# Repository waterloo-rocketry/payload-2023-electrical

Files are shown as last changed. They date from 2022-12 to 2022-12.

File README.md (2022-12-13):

WELCOME TO PAYLOAD: "NOT QUITE DEPLOYABLE"

Here is the folder in the google drive where most of our research happens (if you don't have access, and need it, ask!)
https://drive.google.com/drive/folders/1Cd6_AShmbkWPmAZkzhvAZI7hbHMKju_5?usp=sharing

If you can't find the project you're looking for, make sure to check the branches

CONFLUENCE (but don't expect it to be updated)
https://uwaterloo.atlassian.net/wiki/spaces/ROCKETRY/pages/42574873580/Payload

**How to Start Editing Schematics**
- Clone the "canhw" repo from https://github.com/waterloo-rocketry/canhw
- Enter canhw and make sure you are on the most up to date version of master branch
- Make sure that both the payload-2023-electrical and canhw repos are in the same parent directory! KiCAD will not be able to find our custom libraries otherwise

# 2023 Electrical Overview
Please see the updated .drawio file, which contains a detailed electrical block diagram

The 2023 electrical system is made up of 5 boards:

### GPS board
- Can be found at https://github.com/waterloo-rocketry/canhw/tree/master/gps
- GPS is a very simple board. It gets data from a GPS reciever and forwards it over CAN. 
- Data from GPS board will be the x/y position measurement input to state estimation
- A copy will be mounted on GrandPapa

### Logger board
- Can be found at https://github.com/waterloo-rocketry/canhw/tree/master/logger
- Logger is also a very simple board. It reads in all the CAN messages it sees and saves them to an SD card
- Logger is extremely useful for all sorts of diagnostics, but will allow us to collect all the sensor data as the rocket flies, do some post-flight analysis, and hopefully figure out if state estimation did a good job
- A copy will be mounted on GrandPapa

### Minisensor
- Can be found at https://github.com/waterloo-rocketry/canhw/tree/master/sensor_mini 
- Minisensor gets data from an altimeter, IMU (an accelerometer, magnetometer, and gyroscope packed into one chip) and optionally one or more pressure transmitters, RTDs, strain gauges, the list goes on (there are some generic amplifier circuits that have a variety of uses).
- For its application to payload, we only care about the IMU and altimeter, which provide most of the data to state estimation
- Will be wired to GrandPapa to maximize flexibility and because there's no more space on it lol

### COTS PIC Dev Board (DM320209)
- Datasheet can be found at http://ww1.microchip.com/downloads/en/DeviceDoc/Curiosity_PIC32MZEF2.0_Development_Board_Users_Guide_DS70005400A.pdf
- This beefy boy runs state estimation cause we did not have time to design a second board from scratch and matrix multiplication (which is basically what state estimation is) is really computationally intensive. An NVIDIA GeForce RTX 4090 GPU was proposed as an alternative but was ultimately struck down because "it would cost double payload's yearly budget" and "doesn't obey the 3U Cubesat standard".

### GrandPapa
- Can be found RIGHT HERE under "/GrandPapa_Board"
- GrandPapa is our power management, battery charging, and communications board. It pulls from the rocket to power the payload's systems, and pulls from the payload's battery supply when external power is no longer available. It also manages communication between RocketCAN (the rocket's main communication network) and the payload's internal network. Because CAN is a broadcast protocol (every board sees every message on the network all the time), and payload will be constantly transmitting sensor data, we do not want those messages interfering with whatever is happening on RocketCAN or vice versa
- See the schamtic notes for details on the power path

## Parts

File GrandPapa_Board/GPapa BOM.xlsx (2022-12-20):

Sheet: GrandPapa_Board_20221209
Column1 | Column2 | Column3 | Column4 | Column5 | Column6 | Column7
Source: | C:\Users\joedo\Documents\UW Rocketry\payload-2023-electrical\GrandPapa_Board\GrandPapa_Board.kicad_sch
Date: | 2022-12-09 12:44:19 PM
Tool: | Eeschema (6.0.5)
Generator: | C:\Program Files\KiCad\6.0\bin\scripting\plugins/bom_csv_grouped_by_value_with_fp.py
Component Count: | 94
Ref | Qnty | Value | Cmp name | Footprint | Description | In Stock In Bay
C1, C2, C5, C22, C23, | 5 | 10uF | C_Small | Capacitor_SMD:C_0805_2012Metric_Pad1.18x1.45mm_HandSolder | Unpolarized capacitor, small symbol | 43 in the bay
C3, C6, C12, C13, C14, C21, | 6 | 0.1uF | C_Small | Capacitor_SMD:C_0805_2012Metric_Pad1.18x1.45mm_HandSolder | Unpolarized capacitor, small symbol | 100+ in the bay
C4, | 1 | 5nF | C_Small | Capacitor_SMD:C_0805_2012Metric_Pad1.18x1.45mm_HandSolder | Unpolarized capacitor, small symbol | 0
C7, C9, C10, C11, | 4 | 4.7uF | C | Capacitor_SMD:C_0805_2012Metric_Pad1.18x1.45mm_HandSolder | Unpolarized capacitor | 50~ in the Bay
C8, | 1 | 25pF | C_Small | Capacitor_SMD:C_0805_2012Metric_Pad1.18x1.45mm_HandSolder | Unpolarized capacitor, small symbol | 25 in the Bay
C15, | 1 | 44 uF | C_Small | Capacitor_SMD:C_0805_2012Metric_Pad1.18x1.45mm_HandSolder | Unpolarized capacitor, small symbol | 0
C16, C17, | 2 | 27pF | C_Small | Capacitor_SMD:C_0805_2012Metric_Pad1.18x1.45mm_HandSolder | Unpolarized capacitor, small symbol | 100+ in the Bay
C18, C19, | 2 | 0.1uF 20V | C_Small | Capacitor_SMD:C_0805_2012Metric_Pad1.18x1.45mm_HandSolder | Unpolarized capacitor, small symbol | 49 in the bay
D1, D5, D8, | 3 | 150120BS75000 | LED | LED_SMD:LED_1206_3216Metric_Pad1.42x1.75mm_HandSolder | Light emitting diode | 100+ in bay
D3, D6, | 2 | QBLP650-IW | LED | LED_SMD:LED_1206_3216Metric_Pad1.42x1.75mm_HandSolder | Light emitting diode | 100+ in bay
D4, D7, | 2 | 156120RS75000 | LED | LED_SMD:LED_1206_3216Metric_Pad1.42x1.75mm_HandSolder | Light emitting diode | 100+ in bay
F1, F3, | 2 | 1.5A | Polyfuse | Fuse:Fuse_0805_2012Metric_Pad1.15x1.40mm_HandSolder | Resettable fuse, polymeric positive temperature coefficient
F2, | 1 | 1.2A | Polyfuse | Fuse:Fuse_0805_2012Metric_Pad1.15x1.40mm_HandSolder | Resettable fuse, polymeric positive temperature coefficient
H1, H2, H3, H4, H5, H6, H7, H8, | 8 | MountingHole_Pad | MountingHole_Pad | MountingHole:MountingHole_3.5mm_Pad_Via | Mounting Hole with connection | N/A
J1, | 1 | 3.7V LiPo Single Cell | Conn_01x02_Female | Connector_JST:JST_PH_S2B-PH-K_1x02_P2.00mm_Horizontal | Generic connector, single row, 01x02, script generated (kicad-library-utils/schlib/autogen/connector/)
J2, | 1 | HARWIN_ROCKET | Conn_01x05 | PapaOld:connector_Harwin_M80-5000642 | Generic connector, single row, 01x05, script generated (kicad-library-utils/schlib/autogen/connector/) | N/A
J3, | 1 | Dupont_GPS | Conn_01x06_Female | PapaOld:connector_Harwin_M80-5000642 | Generic connector, single row, 01x06, script generated (kicad-library-utils/schlib/autogen/connector/)
J4, | 1 | HARWIN_MINISENSOR | Conn_01x05 | PapaOld:connector_Harwin_M80-5000642 | Generic connector, single row, 01x05, script generated (kicad-library-utils/schlib/autogen/connector/) | N/A
J5, | 1 | Dupont_Logger | Conn_01x06_Female | PapaOld:connector_Harwin_M80-5000642 | Generic connector, single row, 01x06, script generated (kicad-library-utils/schlib/autogen/connector/)
J6, | 1 | Prog Header | Conn_01x05_Female | Connector_PinHeader_2.54mm:PinHeader_1x05_P2.54mm_Vertical | Generic connector, single row, 01x05, script generated (kicad-library-utils/schlib/autogen/connector/)
J7, | 1 | HARWIN_KALMAN | Conn_01x05 | PapaOld:connector_Harwin_M80-5000642 | Generic connector, single row, 01x05, script generated (kicad-library-utils/schlib/autogen/connector/) | N/A
J11, | 1 | Dupont 01x04_Male | Conn_01x04_Male | Connector_PinHeader_2.54mm:PinHeader_1x04_P2.54mm_Vertical | Generic connector, single row, 01x04, script generated (kicad-library-utils/schlib/autogen/connector/)
L1, | 1 | 5.6uH | L | Inductor_SMD:L_Vishay_IHLP-2020 | Inductor | ORD
L2, | 1 | 4.7uH | L_Small | Inductor_SMD:L_Sumida_CDMC6D28_7.25x6.5mm | Inductor, small symbol | ORD
R1, R23, | 2 | 20mR | R_US | Resistor_SMD:R_1206_3216Metric_Pad1.30x1.75mm_HandSolder | Resistor, US symbol
R2, | 1 | 1MR | R_Small_US | Resistor_SMD:R_0805_2012Metric_Pad1.20x1.40mm_HandSolder | Resistor, small US symbol
R3, R12, R13, R15, | 4 | 100R | R_Small_US | Resistor_SMD:R_0805_2012Metric_Pad1.20x1.40mm_HandSolder | Resistor, small US symbol
R4, | 1 | 2kR | R_Small_US | Resistor_SMD:R_0805_2012Metric_Pad1.20x1.40mm_HandSolder | Resistor, small US symbol
R5, | 1 | 25kR | R_Small_US | Resistor_SMD:R_0805_2012Metric_Pad1.20x1.40mm_HandSolder | Resistor, small US symbol
R6, R20, R21, | 3 | 470R | R_Small_US | Resistor_SMD:R_0805_2012Metric_Pad1.20x1.40mm_HandSolder | Resistor, small US symbol
R7, | 1 | 500R | R_US | Resistor_SMD:R_0805_2012Metric_Pad1.20x1.40mm_HandSolder | Resistor, US symbol
R8, R11, R17, R18, R26, | 5 | 10kR | R_Small_US | Resistor_SMD:R_0805_2012Metric_Pad1.20x1.40mm_HandSolder | Resistor, small US symbol
R9, R10, R22, R24, | 4 | 0 | R_Small_US | Resistor_SMD:R_0805_2012Metric_Pad1.20x1.40mm_HandSolder | Resistor, small US symbol
R14, | 1 | 150R | R_Small_US | Resistor_SMD:R_0805_2012Metric_Pad1.20x1.40mm_HandSolder | Resistor, small US symbol
R16, | 1 | 11kR | R_Small_US | Resistor_SMD:R_0805_2012Metric_Pad1.20x1.40mm_HandSolder | Resistor, small US symbol
R19, | 1 | 70kR | R_Small_US | Resistor_SMD:R_0805_2012Metric_Pad1.20x1.40mm_HandSolder | Resistor, small US symbol
R25, | 1 | 324kR | R_Small_US | Resistor_SMD:R_0805_2012Metric_Pad1.20x1.40mm_HandSolder | Resistor, small US symbol
R27, | 1 | 15kR | R_US | Resistor_SMD:R_0805_2012Metric_Pad1.20x1.40mm_HandSolder | Resistor, US symbol
TH1, | 1 | 10k | Thermistor_NTC | Resistor_SMD:R_0805_2012Metric_Pad1.20x1.40mm_HandSolder | Temperature dependent resistor, negative temperature coefficient | ORD
TP1, TP2, TP3, TP4, TP7, | 5 | TestPoint | TestPoint | Connector_PinHeader_2.54mm:PinHeader_1x01_P2.54mm_Vertical | test point
U1, | 1 | MCP1642B-50I/MS | MCP1642B{slash}D-xx | Package_SO:MSOP-8_3x3mm_P0.65mm | Fixed Output Boost Regulator | ORD
U2, | 1 | BD9E302EFJ | BD9E302EFJ | Package_SO:HTSOP-8-1EP_3.9x4.9mm_P1.27mm_EP2.4x3.2mm |  | ORD
U3, | 1 | MCP73871T-1CCI/ML | MCP73871 | Package_DFN_QFN:QFN-20-1EP_4x4mm_P0.5mm_EP2.5x2.5mm | Single cell, Li-Ion/Li-Po charge management controller | ORD
U4, U6, | 2 | INA180 | INA180 | Package_TO_SOT_SMD:SOT-23-5_HandSoldering | Low- and High-Side Voltage Output, Current-Sense Amplifier
U5, | 1 | FPF2124 | FPF2124 | Package_TO_SOT_SMD:SOT-23-5_HandSoldering |  | ORD
U7, U8, | 2 | MCP2562-E/SN | MCP2562 | Package_SO:SOIC-8_3.9x4.9mm_P1.27mm | High-Speed CAN Transceiver
U9, | 1 | PIC18F26K83 | PIC18F26K83 | Package_SO:SSOP-28_5.3x10.2mm_P0.65mm | 28-Pin, Low-Power, High-Performance Microcontrollers with CAN Technology
U10, | 1 | MCP2515-I/P | MCP2515 | Package_SO:SOIC-18W_7.5x11.6mm_P1.27mm |  | ORD
Y1, | 1 | 12MHz | Crystal | Crystal:Crystal_HC49-4H_Vertical | Two pin crystal | IN STOCK

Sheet: GrandPapa_Board_2022_12_14
_ | Column2 | Column3 | Column4 | Column5 | Column6 | Column7 | Column8
Source: | C:\Users\joedo\Documents\UW Rocketry\payload-2023-electrical\GrandPapa_Board\GrandPapa_Board.kicad_sch
Date: | 2022-12-14 7:13:50 AM
Tool: | Eeschema (6.0.5)
Generator: | C:\Program Files\KiCad\6.0\bin\scripting\plugins/bom_csv_grouped_by_value_with_fp.py
Component Count: | 97
Ref | Qnty | Value | Cmp name | Footprint | Description | In Stock | In Order
C1, C2, C5, C22, C23, | 5 | 10uF | C_Small | Capacitor_SMD:C_0805_2012Metric_Pad1.18x1.45mm_HandSolder | Unpolarized capacitor, small symbol | 43 in the bay | Y
C3, C6, C12, C13, C14, C21, | 6 | 0.1uF | C_Small | Capacitor_SMD:C_0805_2012Metric_Pad1.18x1.45mm_HandSolder | Unpolarized capacitor, small symbol | 100+ in the bay | Y
C4, | 1 | 5nF | C_Small | Capacitor_SMD:C_0805_2012Metric_Pad1.18x1.45mm_HandSolder | Unpolarized capacitor, small symbol | 0 | Y
C7, C9, C10, C11, | 4 | 4.7uF | C | Capacitor_SMD:C_0805_2012Metric_Pad1.18x1.45mm_HandSolder | Unpolarized capacitor | 50~ in the Bay
C8, | 1 | 25pF | C_Small | Capacitor_SMD:C_0805_2012Metric_Pad1.18x1.45mm_HandSolder | Unpolarized capacitor, small symbol | 25 in the Bay
C15, | 1 | 44 uF | C_Small | Capacitor_SMD:C_0805_2012Metric_Pad1.18x1.45mm_HandSolder | Unpolarized capacitor, small symbol | 0 | Y
C16, C17, | 2 | 27pF | C_Small | Capacitor_SMD:C_0805_2012Metric_Pad1.18x1.45mm_HandSolder | Unpolarized capacitor, small symbol | 100+ in the Bay
C18, C19, | 2 | 0.1uF 20V | C_Small | Capacitor_SMD:C_0805_2012Metric_Pad1.18x1.45mm_HandSolder | Unpolarized capacitor, small symbol | 49 in the bay
D1, D5, D8, | 3 | 150120BS75000 | LED | LED_SMD:LED_1206_3216Metric_Pad1.42x1.75mm_HandSolder | Light emitting diode | 100+ in bay
D3, D6, | 2 | QBLP650-IW | LED | LED_SMD:LED_1206_3216Metric_Pad1.42x1.75mm_HandSolder | Light emitting diode | 100+ in bay
D4, D7, | 2 | 156120RS75000 | LED | LED_SMD:LED_1206_3216Metric_Pad1.42x1.75mm_HandSolder | Light emitting diode | 100+ in bay
F1, F2, F3, | 3 | 1.5A | Polyfuse | Fuse:Fuse_1812_4532Metric_Pad1.30x3.40mm_HandSolder | Resettable fuse, polymeric positive temperature coefficient |  | Y
H1, H2, H4, H5, | 4 | MountingHole_Pad | MountingHole_Pad | MountingHole:MountingHole_3.2mm_M3_Pad | Mounting Hole with connection | N/A
H3, H6, H7, H8, | 4 | MountingHole_Pad | MountingHole_Pad | MountingHole:MountingHole_3.5mm_Pad_Via | Mounting Hole with connection | N/A
J1, | 1 | 3.7V LiPo Single Cell | Conn_01x02_Female | Connector_JST:JST_PH_S2B-PH-K_1x02_P2.00mm_Horizontal | Generic connector, single row, 01x02, script generated (kicad-library-utils/schlib/autogen/connector/)
J2, | 1 | HARWIN_ROCKET | Conn_01x05 | PapaOld:connector_Harwin_M80-5000642 | Generic connector, single row, 01x05, script generated (kicad-library-utils/schlib/autogen/connector/) | N/A
J3, | 1 | Dupont_GPS | Conn_01x06_Female | PapaOld:connector_Harwin_M80-5000642 | Generic connector, single row, 01x06, script generated (kicad-library-utils/schlib/autogen/connector/)
J4, | 1 | HARWIN_MINISENSOR | Conn_01x05 | PapaOld:connector_Harwin_M80-5000642 | Generic connector, single row, 01x05, script generated (kicad-library-utils/schlib/autogen/connector/) | N/A
J5, | 1 | Dupont_Logger | Conn_01x06_Female | PapaOld:connector_Harwin_M80-5000642 | Generic connector, single row, 01x06, script generated (kicad-library-utils/schlib/autogen/connector/)
J6, | 1 | PROG Header | Conn_01x05_Female | Connector_PinHeader_2.54mm:PinHeader_1x05_P2.54mm_Vertical | Generic connector, single row, 01x05, script generated (kicad-library-utils/schlib/autogen/connector/)
J7, | 1 | HARWIN_KALMAN | Conn_01x05 | PapaOld:connector_Harwin_M80-5000642 | Generic connector, single row, 01x05, script generated (kicad-library-utils/schlib/autogen/connector/) | N/A
J8, | 1 | Therm EN Jumper | Conn_01x03_Male | Connector_PinHeader_2.54mm:PinHeader_1x03_P2.54mm_Vertical | Generic connector, single row, 01x03, script generated (kicad-library-utils/schlib/autogen/connector/) |  | Y
J11, | 1 | Dupont 01x04_Male | Conn_01x04_Male | Connector_PinHeader_2.54mm:PinHeader_1x04_P2.54mm_Vertical | Generic connector, single row, 01x04, script generated (kicad-library-utils/schlib/autogen/connector/)
L1, | 1 | 5.6uH | L | Inductor_SMD:L_Vishay_IHLP-2020 | Inductor |  | Y
L2, | 1 | 4.7uH | L_Small | Inductor_SMD:L_Sumida_CDMC6D28_7.25x6.5mm | Inductor, small symbol |  | Y
R1, R23, | 2 | 20mR | R_US | Resistor_SMD:R_1206_3216Metric_Pad1.30x1.75mm_HandSolder | Resistor, US symbol
R2, | 1 | 1MR | R_Small_US | Resistor_SMD:R_0805_2012Metric_Pad1.20x1.40mm_HandSolder | Resistor, small US symbol |  | Y
R3, R12, R13, R15, | 4 | 100R | R_Small_US | Resistor_SMD:R_0805_2012Metric_Pad1.20x1.40mm_HandSolder | Resistor, small US symbol |  | Y
R4, R8, R11, R17, R18, R26, R29, | 7 | 10kR | R_Small_US | Resistor_SMD:R_0805_2012Metric_Pad1.20x1.40mm_HandSolder | Resistor, small US symbol
R5, | 1 | 25kR | R_Small_US | Resistor_SMD:R_0805_2012Metric_Pad1.20x1.40mm_HandSolder | Resistor, small US symbol |  | Y
R6, R20, R21, | 3 | 470R | R_Small_US | Resistor_SMD:R_0805_2012Metric_Pad1.20x1.40mm_HandSolder | Resistor, small US symbol
R7, | 1 | 500R | R_US | Resistor_SMD:R_0805_2012Metric_Pad1.20x1.40mm_HandSolder | Resistor, US symbol |  | Y
R9, R10, R22, R24, | 4 | 0 | R_Small_US | Resistor_SMD:R_0805_2012Metric_Pad1.20x1.40mm_HandSolder | Resistor, small US symbol
R14, | 1 | 150R | R_Small_US | Resistor_SMD:R_0805_2012Metric_Pad1.20x1.40mm_HandSolder | Resistor, small US symbol
R16, | 1 | 11kR | R_Small_US | Resistor_SMD:R_0805_2012Metric_Pad1.20x1.40mm_HandSolder | Resistor, small US symbol |  | Y
R19, | 1 | 70kR | R_Small_US | Resistor_SMD:R_0805_2012Metric_Pad1.20x1.40mm_HandSolder | Resistor, small US symbol |  | Y
R25, | 1 | 324kR | R_Small_US | Resistor_SMD:R_0805_2012Metric_Pad1.20x1.40mm_HandSolder | Resistor, small US symbol |  | Y
R27, | 1 | 15kR | R_US | Resistor_SMD:R_0805_2012Metric_Pad1.20x1.40mm_HandSolder | Resistor, US symbol
R28, | 1 | 2.5kR | R_Small_US | Resistor_SMD:R_0805_2012Metric_Pad1.20x1.40mm_HandSolder | Resistor, small US symbol |  | Y
TH1, | 1 | 10k | Thermistor_NTC | Resistor_SMD:R_0805_2012Metric_Pad1.20x1.40mm_HandSolder | Temperature dependent resistor, negative temperature coefficient |  | Y
TP1, TP2, TP3, TP4, TP7, | 5 | TestPoint | TestPoint | Connector_PinHeader_2.54mm:PinHeader_1x01_P2.54mm_Vertical | test point |  | Y
U1, | 1 | MCP1642B-50I/MS | MCP1642B{slash}D-xx | Package_SO:MSOP-8_3x3mm_P0.65mm | Fixed Output Boost Regulator |  | Y
U2, | 1 | BD9E302EFJ | BD9E302EFJ | Package_SO:HTSOP-8-1EP_3.9x4.9mm_P1.27mm_EP2.4x3.2mm |  |  | Y
U3, | 1 | MCP73871T-1CCI/ML | MCP73871 | Package_DFN_QFN:QFN-20-1EP_4x4mm_P0.5mm_EP2.5x2.5mm | Single cell, Li-Ion/Li-Po charge management controller |  | Y
U4, U6, | 2 | INA180 | INA180 | Package_TO_SOT_SMD:SOT-23-5_HandSoldering | Low- and High-Side Voltage Output, Current-Sense Amplifier
U5, | 1 | FPF2124 | FPF2124 | Package_TO_SOT_SMD:SOT-23-5_HandSoldering |  |  | Y
U7, U8, | 2 | MCP2562-E/SN | MCP2562 | Package_SO:SOIC-8_3.9x4.9mm_P1.27mm | High-Speed CAN Transceiver
U9, | 1 | PIC18F26K83 | PIC18F26K83 | Package_SO:SSOP-28_5.3x10.2mm_P0.65mm | 28-Pin, Low-Power, High-Performance Microcontrollers with CAN Technology
U10, | 1 | MCP2515-I/P | MCP2515 | Package_SO:SOIC-18W_7.5x11.6mm_P1.27mm
Y1, | 1 | 12MHz | Crystal | Crystal:Crystal_HC49-4H_Vertical | Two pin crystal

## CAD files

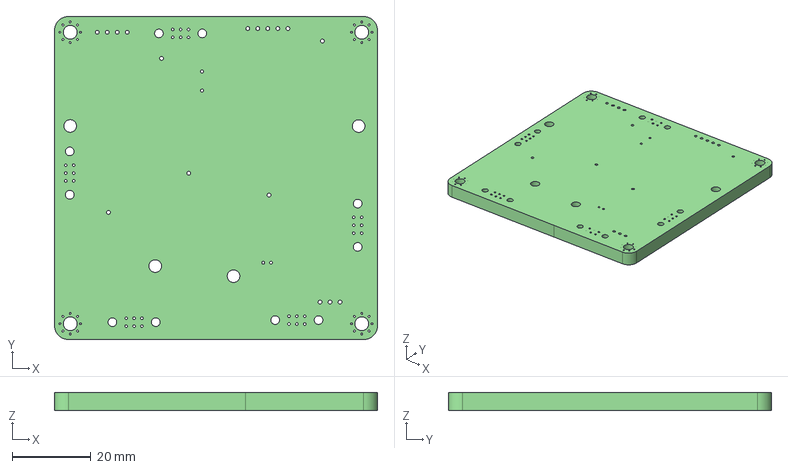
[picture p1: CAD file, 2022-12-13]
GrandPapa_Board/GrandPapa_Board.step
82.0 x 82.0 x 4.69 mm

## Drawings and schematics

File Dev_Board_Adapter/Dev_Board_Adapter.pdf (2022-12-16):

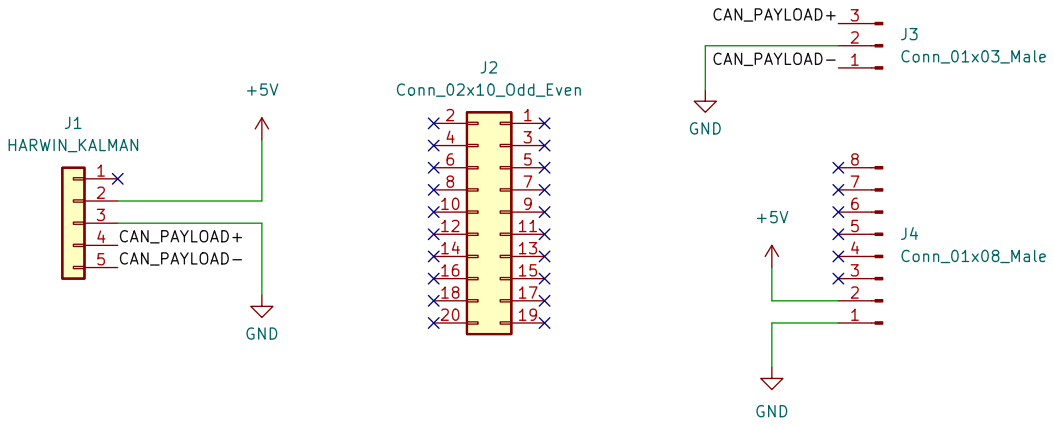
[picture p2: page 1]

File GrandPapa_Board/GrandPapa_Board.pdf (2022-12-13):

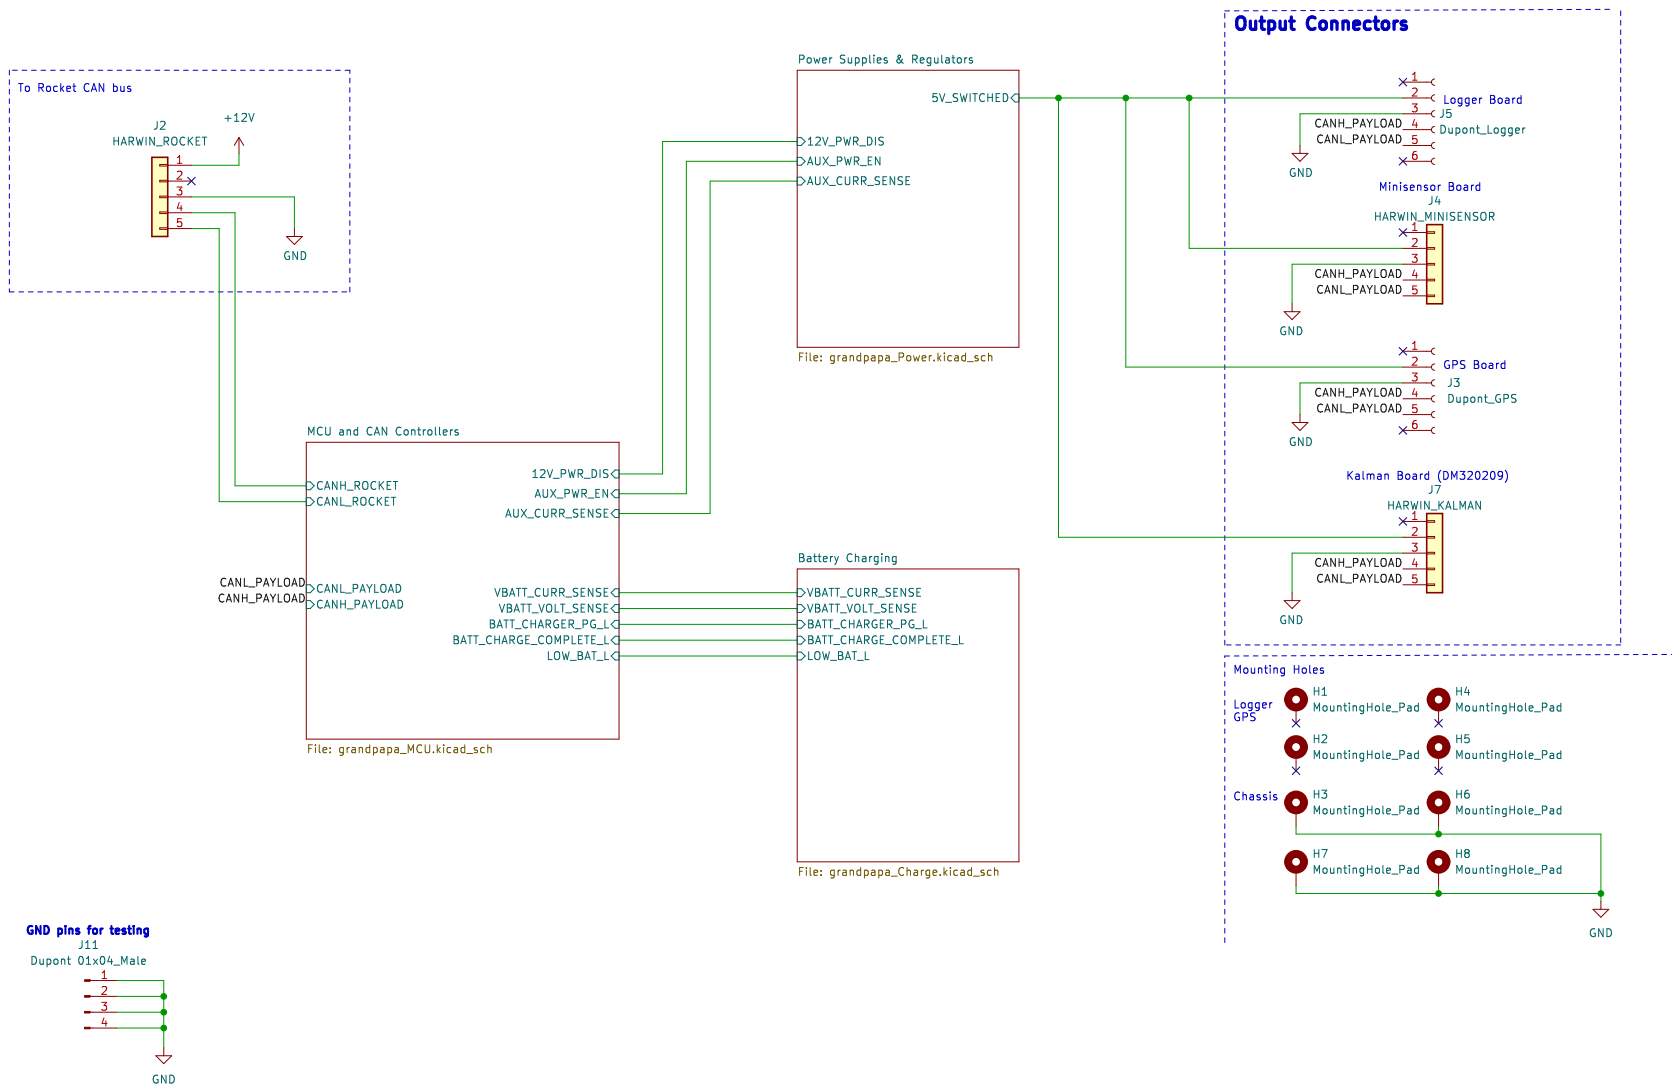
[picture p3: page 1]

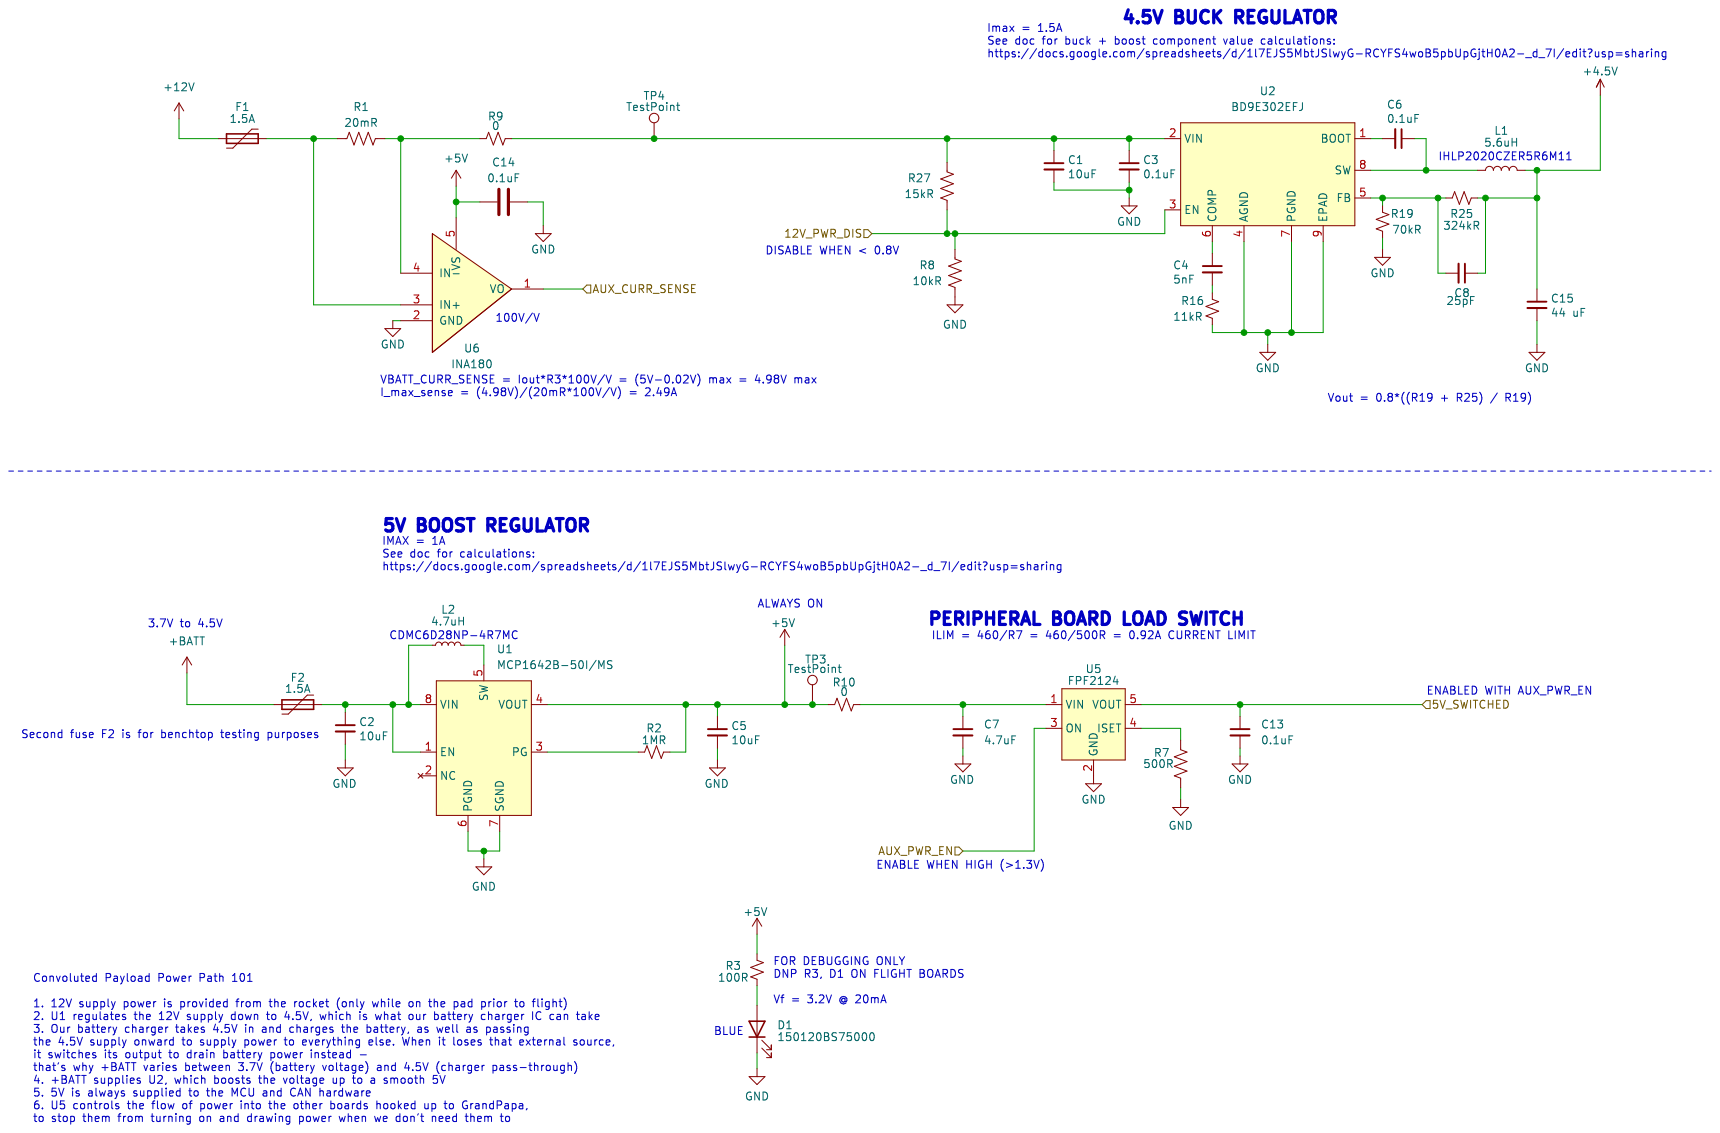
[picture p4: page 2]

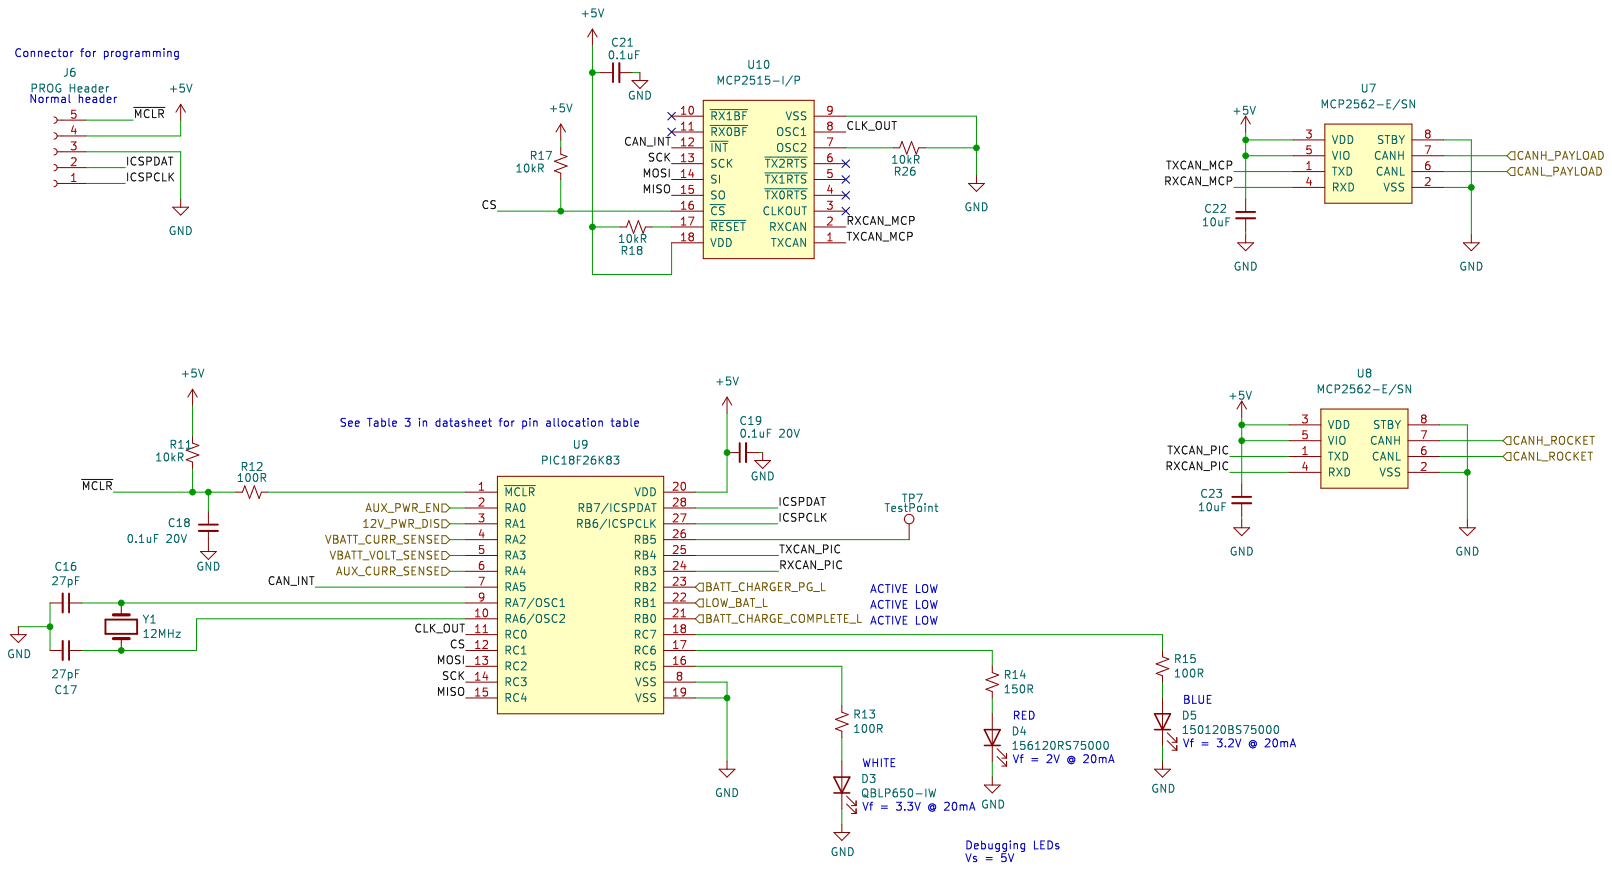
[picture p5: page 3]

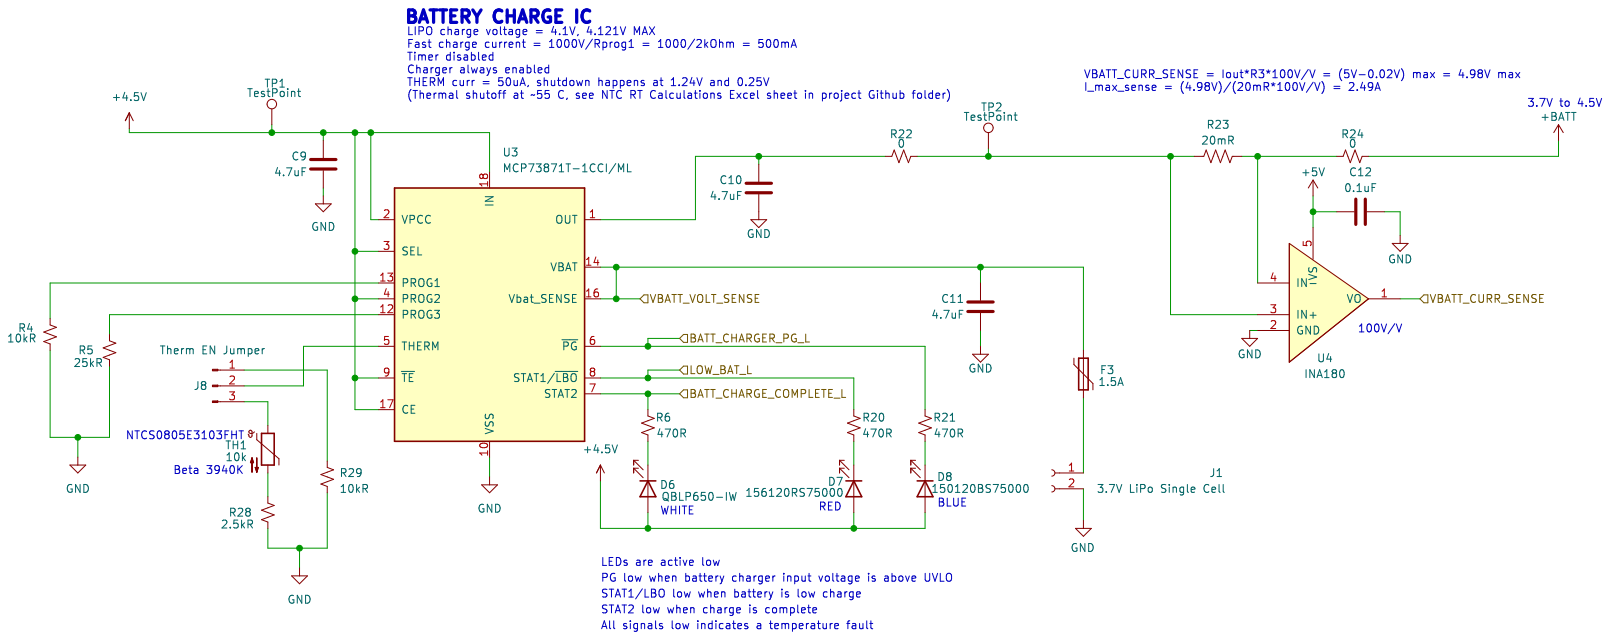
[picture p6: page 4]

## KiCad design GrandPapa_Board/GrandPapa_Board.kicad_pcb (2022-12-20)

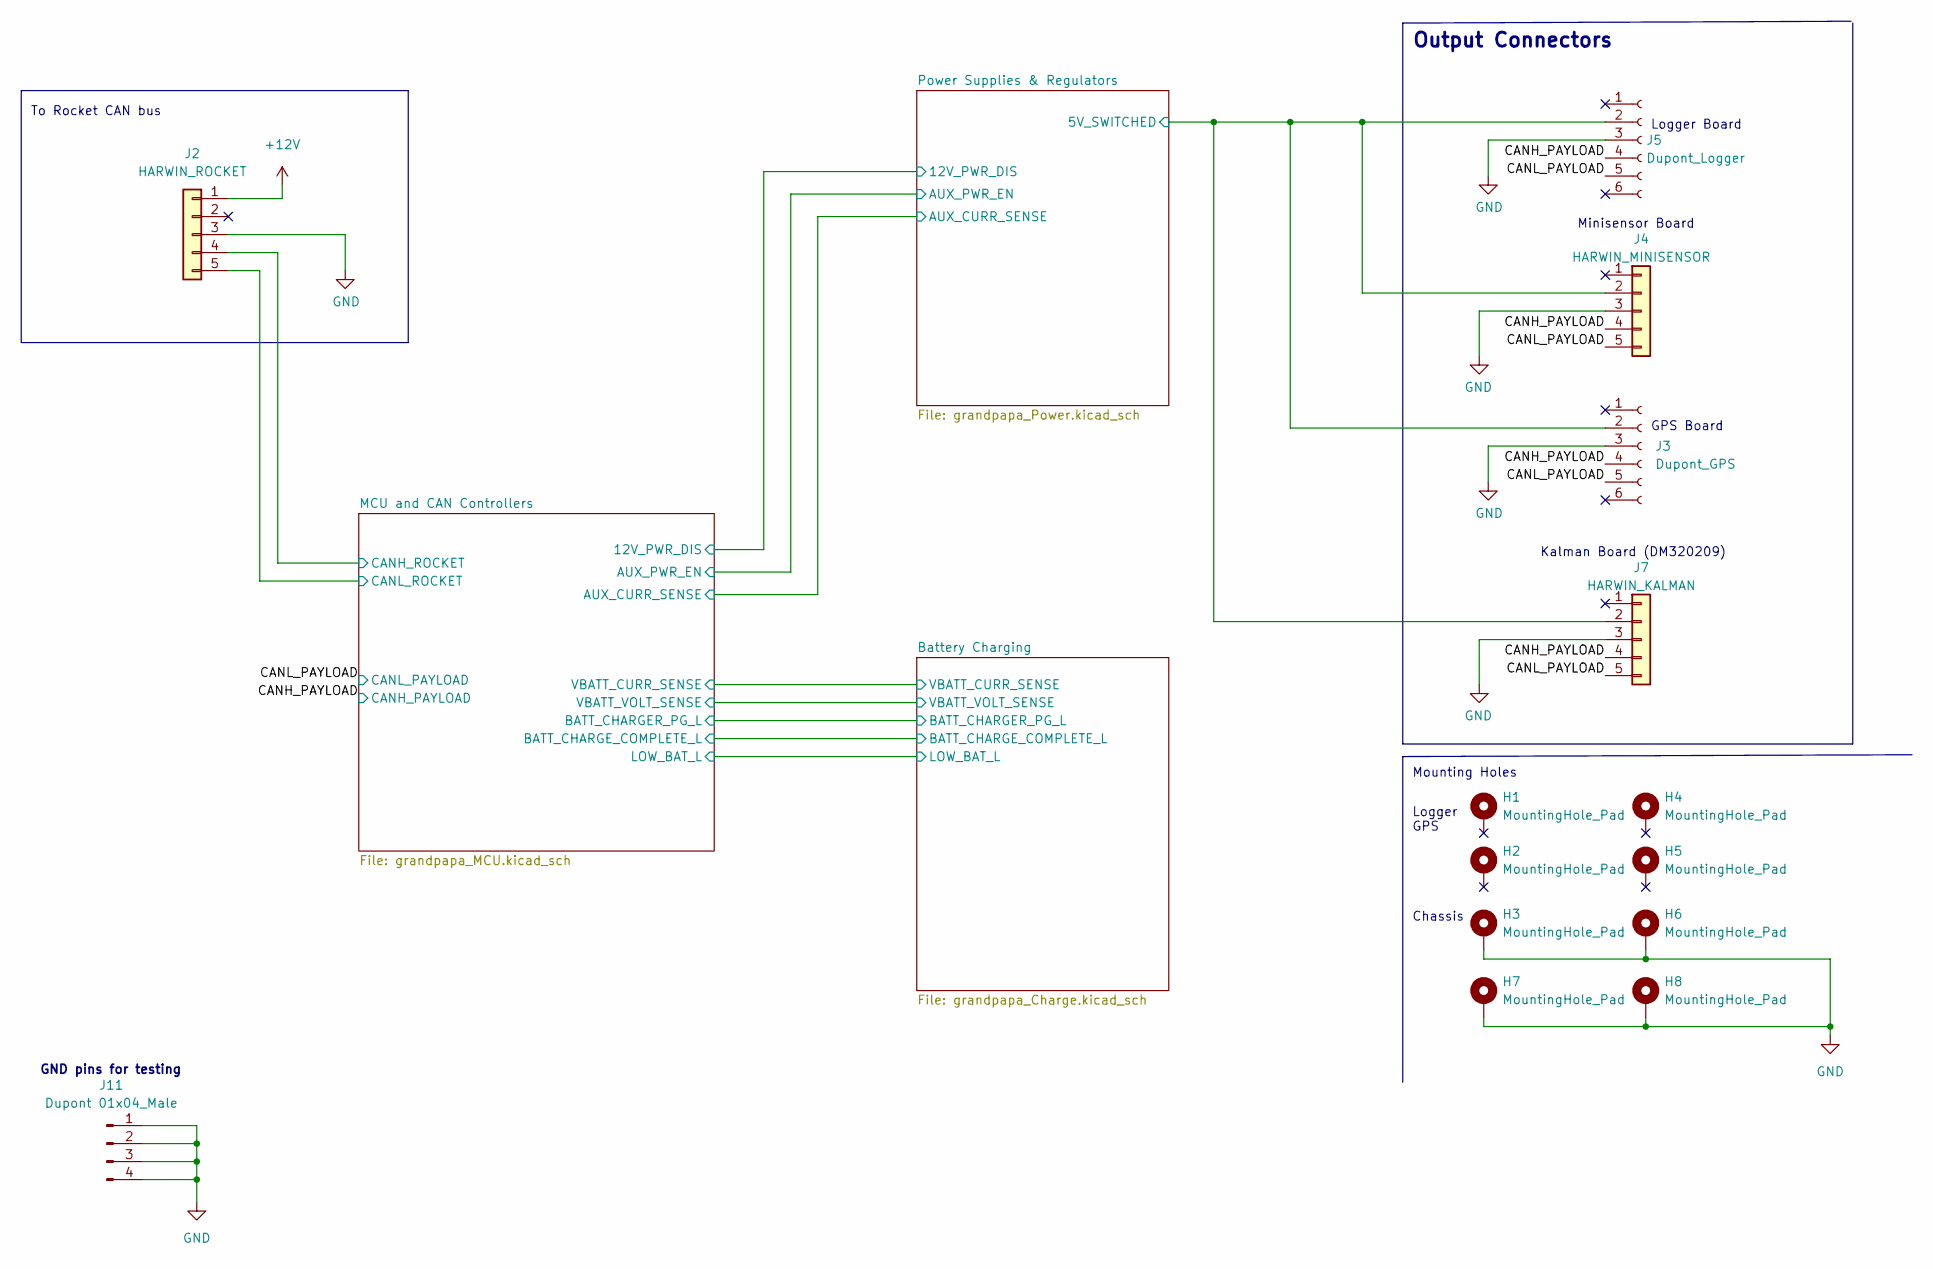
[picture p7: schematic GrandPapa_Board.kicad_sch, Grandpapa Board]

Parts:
H1, H2, H4, H5: MountingHole_Pad; MountingHole_3.2mm_M3_Pad
H3, H6, H7, H8: MountingHole_Pad; MountingHole_3.5mm_Pad_Via
J2: HARWIN_ROCKET; connector_Harwin_M80-5000642
J3: Dupont_GPS; connector_Harwin_M80-5000642
J4: HARWIN_MINISENSOR; connector_Harwin_M80-5000642
J5: Dupont_Logger; connector_Harwin_M80-5000642
J7: HARWIN_KALMAN; connector_Harwin_M80-5000642
J11: Dupont 01x04_Male; PinHeader_1x04_P2.54mm_Vertical

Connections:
+12V: J2.1; also elsewhere on the board
/CANH_PAYLOAD: J3.4, J4.4, J5.4, J7.4; also elsewhere on the board
/CANL_PAYLOAD: J3.5, J4.5, J5.5, J7.5; also elsewhere on the board
/MCU and CAN Controllers/CANH_ROCKET: J2.4; also elsewhere on the board
/MCU and CAN Controllers/CANL_ROCKET: J2.5; also elsewhere on the board
/Power Supplies & Regulators/5V_SWITCHED: J3.2, J4.2, J5.2, J7.2; also elsewhere on the board
GND: H3.1, H6.1, H7.1, H8.1, J2.3, J3.3, J4.3, J5.3, J7.3, J11.1, J11.2, J11.3, J11.4; also elsewhere on the board

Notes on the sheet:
Logger Board
Kalman Board (DM320209)
GPS Board
Mounting Holes
Output Connectors
Minisensor Board
Chassis
To Rocket CAN bus
GND pins for testing
Logger GPS

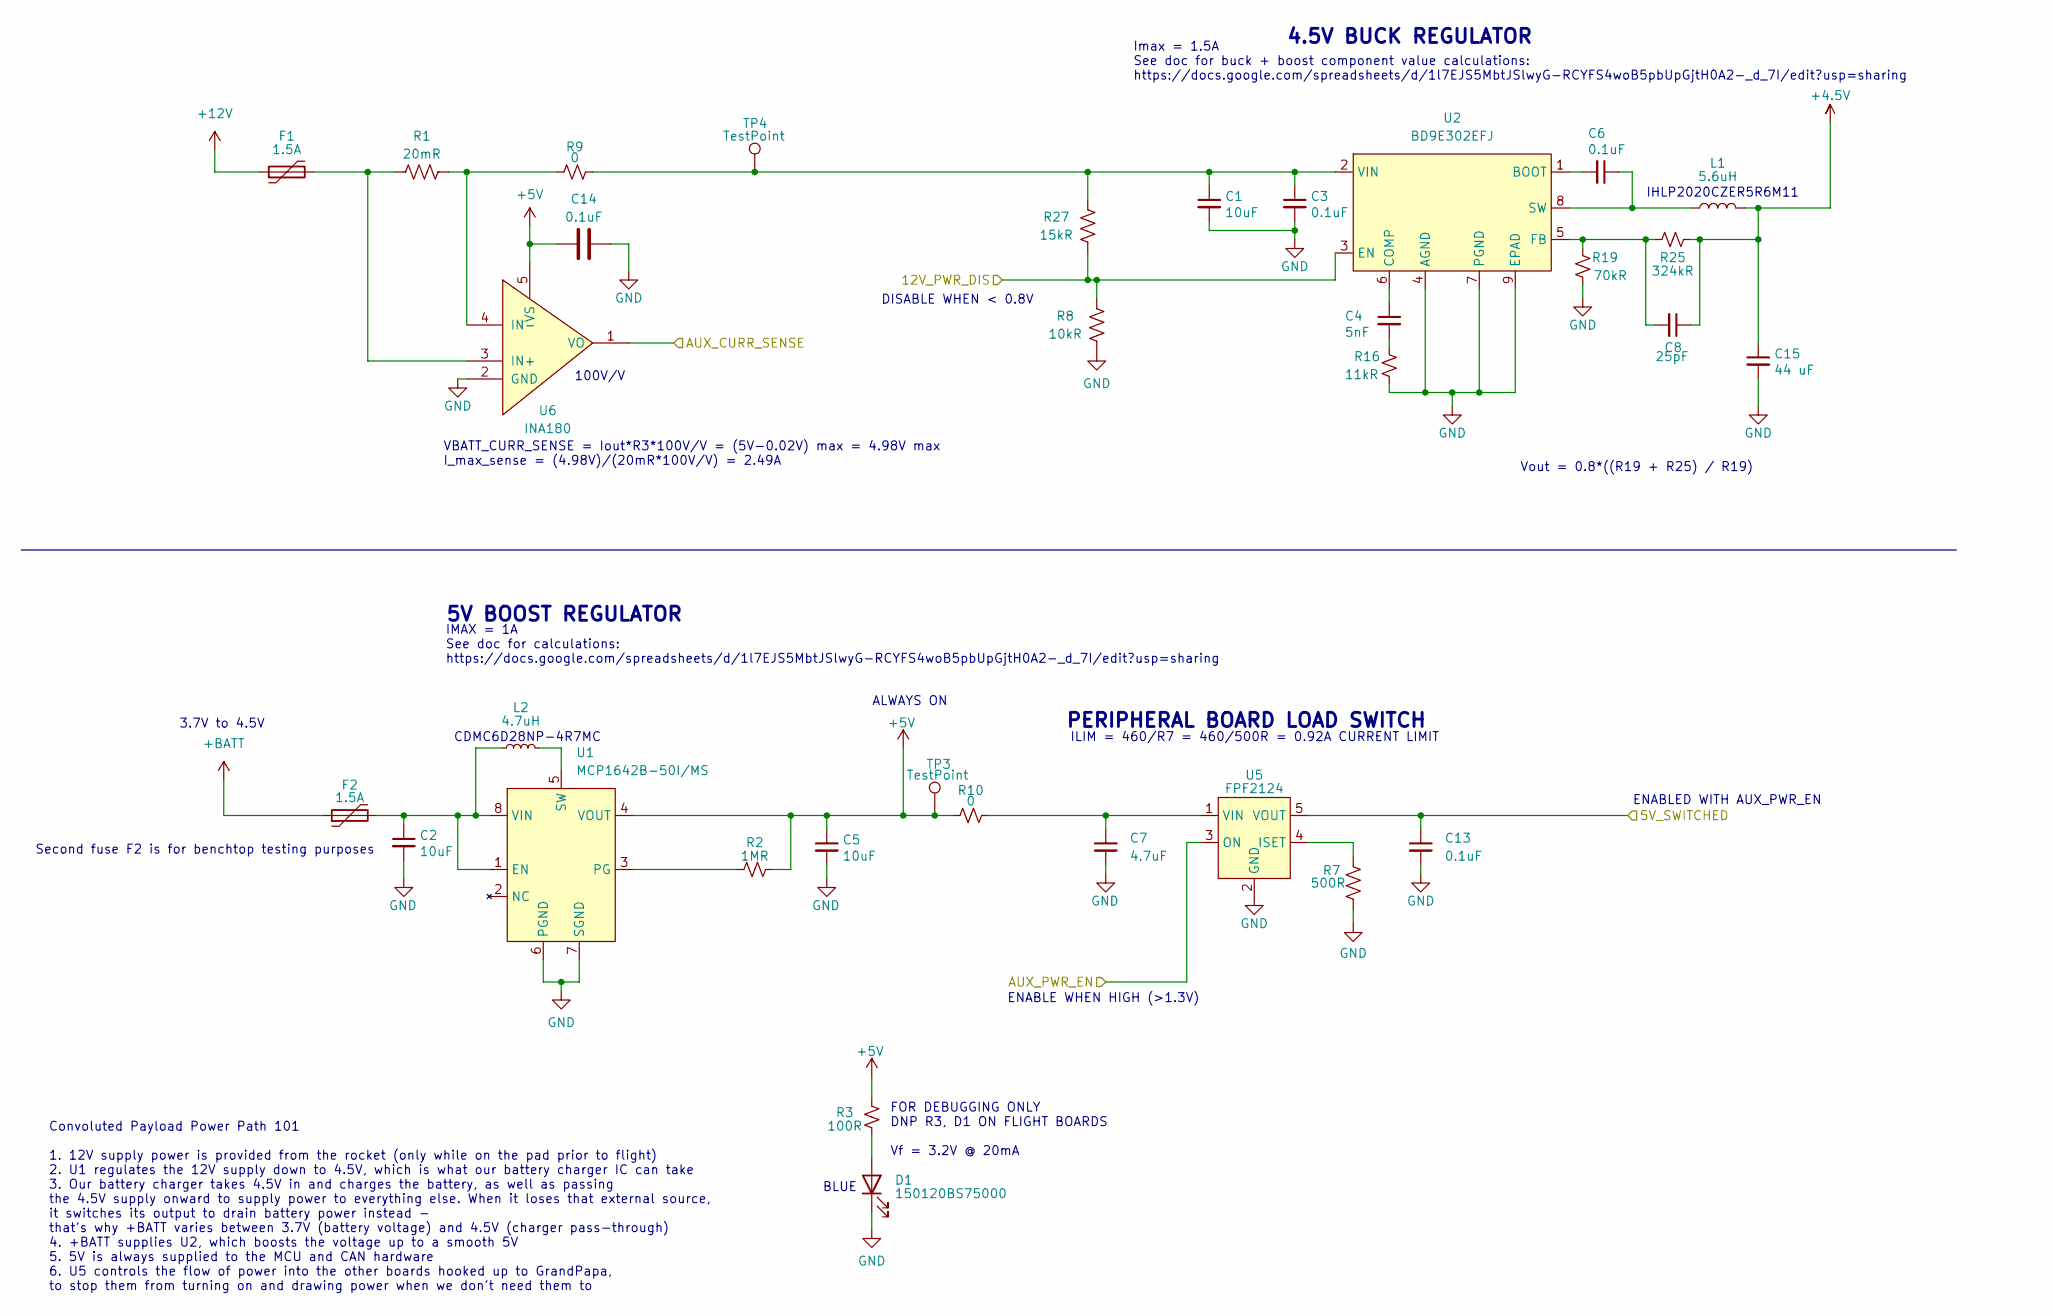
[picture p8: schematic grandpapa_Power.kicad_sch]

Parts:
C1, C2, C5: 10uF; C_0805_2012Metric_Pad1.18x1.45mm_HandSolder
C3, C6, C13, C14: 0.1uF; C_0805_2012Metric_Pad1.18x1.45mm_HandSolder
C4: 5nF; C_0805_2012Metric_Pad1.18x1.45mm_HandSolder
C7: 4.7uF; C_0805_2012Metric_Pad1.18x1.45mm_HandSolder
C8: 25pF; C_0805_2012Metric_Pad1.18x1.45mm_HandSolder
C15: 44 uF; C_0805_2012Metric_Pad1.18x1.45mm_HandSolder
D1: 150120BS75000; LED_1206_3216Metric_Pad1.42x1.75mm_HandSolder
F1, F2: 1.5A; Fuse_1812_4532Metric_Pad1.30x3.40mm_HandSolder
L1: 5.6uH; L_Vishay_IHLP-2020
L2: 4.7uH; L_Sumida_CDMC6D28_7.25x6.5mm
R1: 20mR; R_1206_3216Metric_Pad1.30x1.75mm_HandSolder
R2: 1MR; R_0805_2012Metric_Pad1.20x1.40mm_HandSolder
R3: 100R; R_0805_2012Metric_Pad1.20x1.40mm_HandSolder
R7: 500R; R_0805_2012Metric_Pad1.20x1.40mm_HandSolder
R8: 10kR; R_0805_2012Metric_Pad1.20x1.40mm_HandSolder
R9, R10: 0; R_0805_2012Metric_Pad1.20x1.40mm_HandSolder
R16: 11kR; R_0805_2012Metric_Pad1.20x1.40mm_HandSolder
R19: 70kR; R_0805_2012Metric_Pad1.20x1.40mm_HandSolder
R25: 324kR; R_0805_2012Metric_Pad1.20x1.40mm_HandSolder
R27: 15kR; R_0805_2012Metric_Pad1.20x1.40mm_HandSolder
TP3, TP4: TestPoint; PinHeader_1x01_P2.54mm_Vertical
U1: MCP1642B-50I/MS; MSOP-8_3x3mm_P0.65mm
U2: BD9E302EFJ; HTSOP-8-1EP_3.9x4.9mm_P1.27mm_EP2.4x3.2mm
U5: FPF2124; SOT-23-5_HandSoldering
U6: INA180; SOT-23-5_HandSoldering

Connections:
+4.5V: C8.1, C15.1, L1.2, R25.2; also elsewhere on the board
+5V: C5.1, C14.2, R2.1, R3.2, R10.1, TP3.1, U1.4 (VOUT), U6.5 (VS); also elsewhere on the board
+12V: F1.1; also elsewhere on the board
+BATT: F2.1; also elsewhere on the board
/MCU and CAN Controllers/12V_PWR_DIS: R8.1, R27.2, U2.3 (EN); also elsewhere on the board
/MCU and CAN Controllers/AUX_CURR_SENSE: U6.1 (VO); also elsewhere on the board
/MCU and CAN Controllers/AUX_PWR_EN: U5.3 (ON); also elsewhere on the board
/Power Supplies & Regulators/5V_SWITCHED: C13.1, U5.5 (VOUT); also elsewhere on the board
GND: C1.2, C2.2, C3.2, C5.2, C7.2, C13.2, C14.1, C15.2, D1.1 (K), R7.2, R8.2, R16.1, R19.2, U1.6 (PGND), U1.7 (SGND), U2.4 (AGND), U2.7 (PGND), U2.9 (EPAD), U5.2 (GND), U6.2 (GND); also elsewhere on the board
unnamed: C1.1, C3.1, R9.2, R27.1, TP4.1, U2.2 (VIN)
unnamed: C2.1, F2.2, L2.1, U1.1 (EN), U1.8 (VIN)
unnamed: C4.1, U2.6 (COMP)
unnamed: C4.2, R16.2
unnamed: C6.1, L1.1, U2.8 (SW)
unnamed: C6.2, U2.1 (BOOT)
unnamed: C7.1, R10.2, U5.1 (VIN)
unnamed: C8.2, R19.1, R25.1, U2.5 (FB)
unnamed: D1.2 (A), R3.1
unnamed: F1.2, R1.2, U6.3 (IN+)
unnamed: L2.2, U1.5 (SW)
unnamed: R1.1, R9.1, U6.4 (IN-)
unnamed: R2.2, U1.3 (PG)
unnamed: R7.1, U5.4 (ISET)

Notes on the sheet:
ILIM = 460/R7 = 460/500R = 0.92A CURRENT LIMIT
DISABLE WHEN < 0.8V
5V BOOST REGULATOR
4.5V BUCK REGULATOR
ALWAYS ON
PERIPHERAL BOARD LOAD SWITCH
BLUE
Vout = 0.8*((R19 + R25) / R19)
100V/V
3.7V to 4.5V
Imax = 1.5A See doc for buck + boost component value calculations: https://docs.google.com/spreadsheets/d/1l7EJS5MbtJSlwyG-RCYFS4woB5pbUpGjtH0A2-_d_7I/edit?usp=sharing
ENABLED WITH AUX_PWR_EN
FOR DEBUGGING ONLY DNP R3, D1 ON FLIGHT BOARDS Vf = 3.2V @ 20mA
VBATT_CURR_SENSE = Iout*R3*100V/V = (5V-0.02V) max = 4.98V max I_max_sense = (4.98V)/(20mR*100V/V) = 2.49A
ENABLE WHEN HIGH (>1.3V)
IHLP2020CZER5R6M11
CDMC6D28NP-4R7MC
IMAX = 1A See doc for calculations: https://docs.google.com/spreadsheets/d/1l7EJS5MbtJSlwyG-RCYFS4woB5pbUpGjtH0A2-_d_7I/edit?usp=sharing
Convoluted Payload Power Path 101 1. 12V supply power is provided from the rocket (only while on the pad prior to flight) 2. U1 regulates the 12V supply down to 4.5V, which is what our battery charger IC can take 3. Our battery charger takes 4.5V in and charges the battery, as well as passing the 4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
Second fuse F2 is for benchtop testing purposes

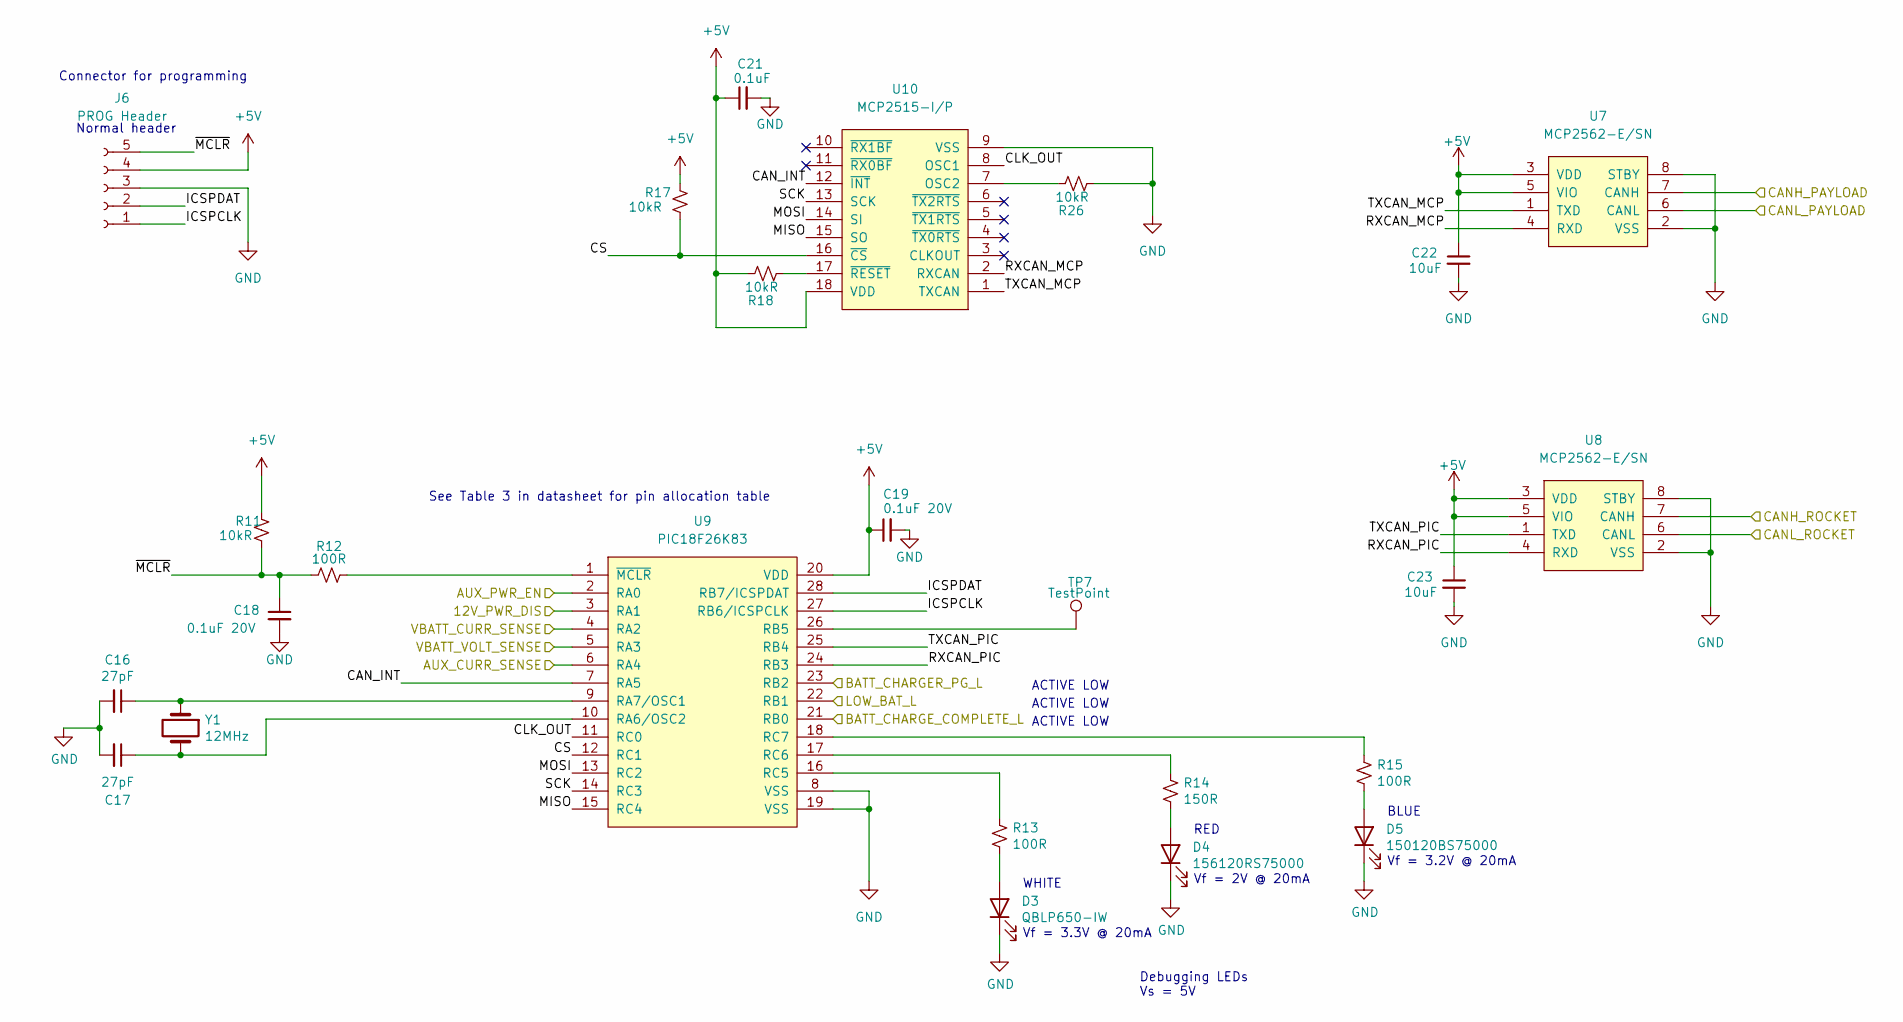
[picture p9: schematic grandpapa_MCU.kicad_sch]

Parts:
C16, C17: 27pF; C_0805_2012Metric_Pad1.18x1.45mm_HandSolder
C18, C19: 0.1uF 20V; C_0805_2012Metric_Pad1.18x1.45mm_HandSolder
C21: 0.1uF; C_0805_2012Metric_Pad1.18x1.45mm_HandSolder
C22, C23: 10uF; C_0805_2012Metric_Pad1.18x1.45mm_HandSolder
D3: QBLP650-IW; LED_1206_3216Metric_Pad1.42x1.75mm_HandSolder
D4: 156120RS75000; LED_1206_3216Metric_Pad1.42x1.75mm_HandSolder
D5: 150120BS75000; LED_1206_3216Metric_Pad1.42x1.75mm_HandSolder
J6: PROG Header; PinHeader_1x05_P2.54mm_Vertical
R11, R17, R18, R26: 10kR; R_0805_2012Metric_Pad1.20x1.40mm_HandSolder
R12, R13, R15: 100R; R_0805_2012Metric_Pad1.20x1.40mm_HandSolder
R14: 150R; R_0805_2012Metric_Pad1.20x1.40mm_HandSolder
TP7: TestPoint; PinHeader_1x01_P2.54mm_Vertical
U7, U8: MCP2562-E/SN; SOIC-8_3.9x4.9mm_P1.27mm
U9: PIC18F26K83; SSOP-28_5.3x10.2mm_P0.65mm
U10: MCP2515-I/P; SOIC-18W_7.5x11.6mm_P1.27mm
Y1: 12MHz; Crystal_HC49-4H_Vertical

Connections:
+5V: C19.1, C21.1, C22.1, C23.1, J6.4, R11.1, R17.1, R18.1, U7.3 (VDD), U7.5 (VIO), U8.3 (VDD), U8.5 (VIO), U9.20 (VDD), U10.18 (VDD); also elsewhere on the board
/Battery Charging/BATT_CHARGER_PG_L: U9.23 (RB2); also elsewhere on the board
/Battery Charging/BATT_CHARGE_COMPLETE_L: U9.21 (RB0); also elsewhere on the board
/Battery Charging/LOW_BAT_L: U9.22 (RB1); also elsewhere on the board
/Battery Charging/VBATT_CURR_SENSE: U9.4 (RA2); also elsewhere on the board
/Battery Charging/VBATT_VOLT_SENSE: U9.5 (RA3); also elsewhere on the board
/CANH_PAYLOAD: U7.7 (CANH); also elsewhere on the board
/CANL_PAYLOAD: U7.6 (CANL); also elsewhere on the board
/MCU and CAN Controllers/12V_PWR_DIS: U9.3 (RA1); also elsewhere on the board
/MCU and CAN Controllers/AUX_CURR_SENSE: U9.6 (RA4); also elsewhere on the board
/MCU and CAN Controllers/AUX_PWR_EN: U9.2 (RA0); also elsewhere on the board
/MCU and CAN Controllers/CANH_ROCKET: U8.7 (CANH); also elsewhere on the board
/MCU and CAN Controllers/CANL_ROCKET: U8.6 (CANL); also elsewhere on the board
/MCU and CAN Controllers/CAN_INT: U9.7 (RA5), U10.12 (~INT)
/MCU and CAN Controllers/CLK_OUT: U9.11 (RC0), U10.8 (OSC1)
/MCU and CAN Controllers/CS: R17.2, U9.12 (RC1), U10.16 (~CS)
/MCU and CAN Controllers/ICSPCLK: J6.1, U9.27 (RB6/ICSPCLK)
/MCU and CAN Controllers/ICSPDAT: J6.2, U9.28 (RB7/ICSPDAT)
/MCU and CAN Controllers/MISO: U9.15 (RC4), U10.15 (SO)
/MCU and CAN Controllers/MOSI: U9.13 (RC2), U10.14 (SI)
/MCU and CAN Controllers/RXCAN_MCP: U7.4 (RXD), U10.2 (RXCAN)
/MCU and CAN Controllers/RXCAN_PIC: U8.4 (RXD), U9.24 (RB3)
/MCU and CAN Controllers/SCK: U9.14 (RC3), U10.13 (SCK)
/MCU and CAN Controllers/TXCAN_MCP: U7.1 (TXD), U10.1 (TXCAN)
/MCU and CAN Controllers/TXCAN_PIC: U8.1 (TXD), U9.25 (RB4)
/MCU and CAN Controllers/~MCLR: C18.1, J6.5, R11.2, R12.1
GND: C16.2, C17.2, C18.2, C19.2, C21.2, C22.2, C23.2, D3.1 (K), D4.1 (K), D5.1 (K), J6.3, R26.2, U7.2 (VSS), U7.8 (STBY), U8.2 (VSS), U8.8 (STBY), U9.8 (VSS), U9.19 (VSS), U10.9 (VSS); also elsewhere on the board
unnamed: C16.1, U9.9 (RA7/OSC1), Y1.1
unnamed: C17.1, U9.10 (RA6/OSC2), Y1.2
unnamed: D3.2 (A), R13.2
unnamed: D4.2 (A), R14.2
unnamed: D5.2 (A), R15.2
unnamed: R12.2, U9.1 (~MCLR)
unnamed: R13.1, U9.16 (RC5)
unnamed: R14.1, U9.17 (RC6)
unnamed: R15.1, U9.18 (RC7)
unnamed: R18.2, U10.17 (~RESET)
unnamed: R26.1, U10.7 (OSC2)
unnamed: TP7.1, U9.26 (RB5)

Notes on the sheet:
Vf = 3.2V @ 20mA
Vf = 3.3V @ 20mA
ACTIVE LOW
See Table 3 in datasheet for pin allocation table
BLUE
RED
Vf = 2V @ 20mA
WHITE
Debugging LEDs Vs = 5V
Normal header
Connector for programming

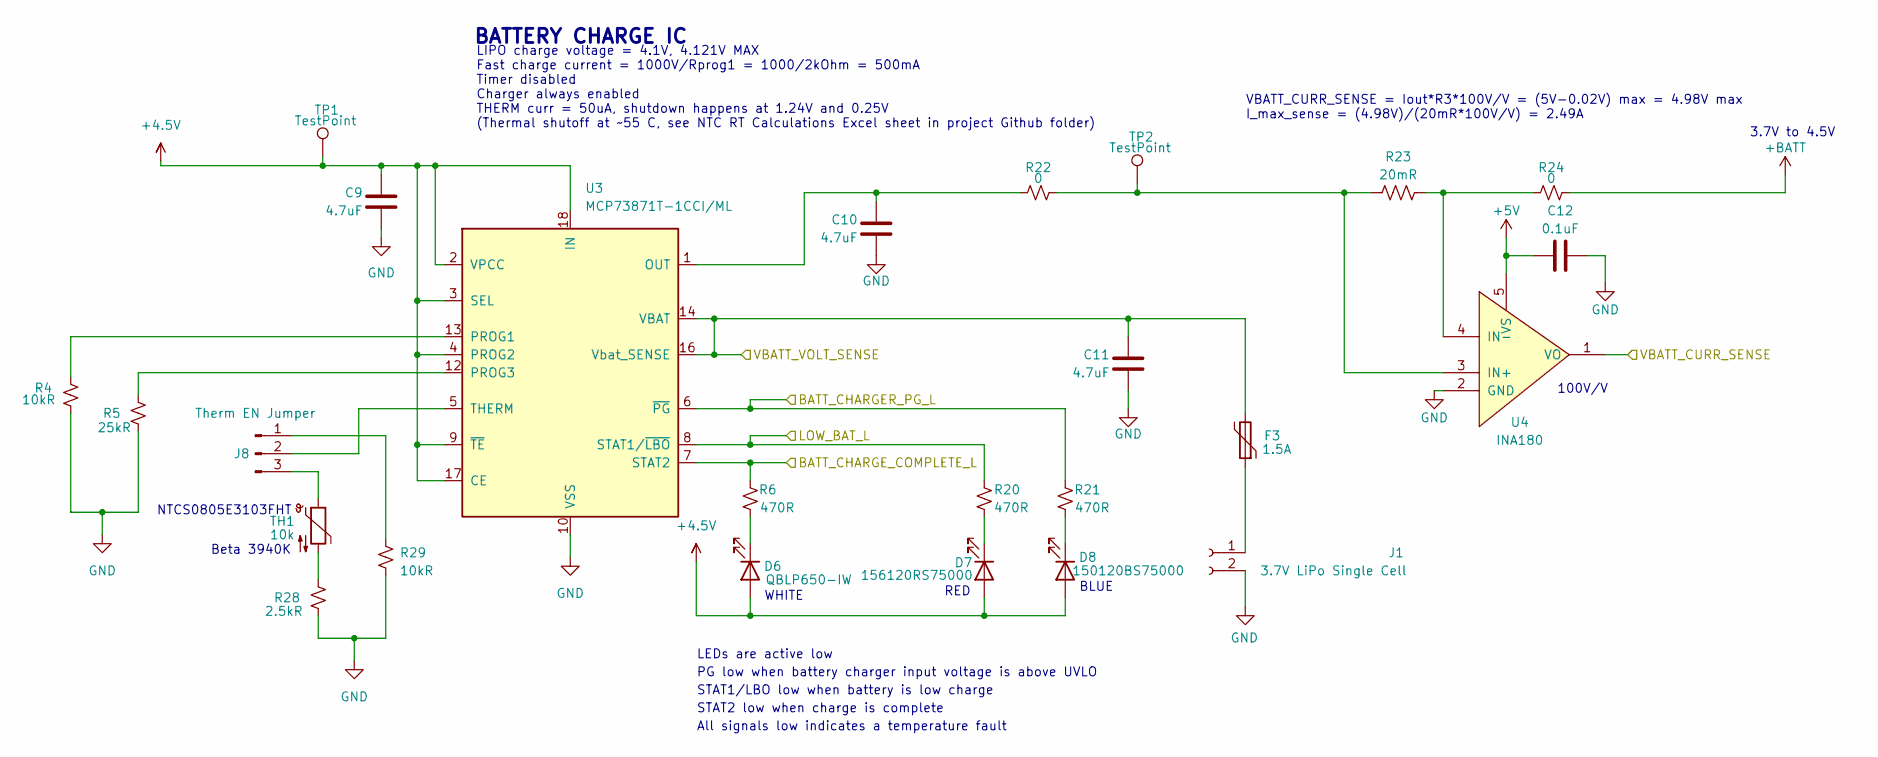
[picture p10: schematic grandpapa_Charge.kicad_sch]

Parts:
C9, C10, C11: 4.7uF; C_0805_2012Metric_Pad1.18x1.45mm_HandSolder
C12: 0.1uF; C_0805_2012Metric_Pad1.18x1.45mm_HandSolder
D6: QBLP650-IW; LED_1206_3216Metric_Pad1.42x1.75mm_HandSolder
D7: 156120RS75000; LED_1206_3216Metric_Pad1.42x1.75mm_HandSolder
D8: 150120BS75000; LED_1206_3216Metric_Pad1.42x1.75mm_HandSolder
F3: 1.5A; Fuse_1812_4532Metric_Pad1.30x3.40mm_HandSolder
J1: 3.7V LiPo Single Cell; JST_PH_S2B-PH-K_1x02_P2.00mm_Horizontal
J8: Therm EN Jumper; PinHeader_1x03_P2.54mm_Vertical
R4, R29: 10kR; R_0805_2012Metric_Pad1.20x1.40mm_HandSolder
R5: 25kR; R_0805_2012Metric_Pad1.20x1.40mm_HandSolder
R6, R20, R21: 470R; R_0805_2012Metric_Pad1.20x1.40mm_HandSolder
R22, R24: 0; R_0805_2012Metric_Pad1.20x1.40mm_HandSolder
R23: 20mR; R_1206_3216Metric_Pad1.30x1.75mm_HandSolder
R28: 2.5kR; R_0805_2012Metric_Pad1.20x1.40mm_HandSolder
TH1: 10k; R_0805_2012Metric_Pad1.20x1.40mm_HandSolder
TP1, TP2: TestPoint; PinHeader_1x01_P2.54mm_Vertical
U3: MCP73871T-1CCI/ML; QFN-20-1EP_4x4mm_P0.5mm_EP2.5x2.5mm
U4: INA180; SOT-23-5_HandSoldering

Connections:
+4.5V: C9.1, D6.2 (A), D7.2 (A), D8.2 (A), TP1.1, U3.2 (VPCC), U3.3 (SEL), U3.4 (PROG2), U3.9 (~TE), U3.17 (CE), U3.18 (IN), U3.19 (IN); also elsewhere on the board
+5V: C12.2, U4.5 (VS); also elsewhere on the board
+BATT: R24.2; also elsewhere on the board
/Battery Charging/BATT_CHARGER_PG_L: R21.2, U3.6 (~PG); also elsewhere on the board
/Battery Charging/BATT_CHARGE_COMPLETE_L: R6.2, U3.7 (STAT2); also elsewhere on the board
/Battery Charging/LOW_BAT_L: R20.1, U3.8 (STAT1/~LBO); also elsewhere on the board
/Battery Charging/VBATT_CURR_SENSE: U4.1 (VO); also elsewhere on the board
/Battery Charging/VBATT_VOLT_SENSE: C11.1, F3.2, U3.14 (VBAT), U3.15 (VBAT), U3.16 (Vbat_SENSE); also elsewhere on the board
GND: C9.2, C10.2, C11.2, C12.1, J1.2, R4.2, R5.2, R28.2, R29.2, U3.10 (VSS), U3.11 (VSS), U3.21 (VSS), U4.2 (GND); also elsewhere on the board
unnamed: C10.1, R22.1, U3.1 (OUT), U3.20 (OUT)
unnamed: D6.1 (K), R6.1
unnamed: D7.1 (K), R20.2
unnamed: D8.1 (K), R21.1
unnamed: F3.1, J1.1
unnamed: J8.1, R29.1
unnamed: J8.2, U3.5 (THERM)
unnamed: J8.3, TH1.1
unnamed: R4.1, U3.13 (PROG1)
unnamed: R5.1, U3.12 (PROG3)
unnamed: R22.2, R23.2, TP2.1, U4.3 (IN+)
unnamed: R23.1, R24.1, U4.4 (IN-)
unnamed: R28.1, TH1.2

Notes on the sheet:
BLUE
All signals low indicates a temperature fault
Beta 3940K
STAT1/LBO low when battery is low charge
100V/V
STAT2 low when charge is complete
LEDs are active low
3.7V to 4.5V
RED
NTCS0805E3103FHT
PG low when battery charger input voltage is above UVLO
BATTERY CHARGE IC
WHITE
LIPO charge voltage = 4.1V, 4.121V MAX Fast charge current = 1000V/Rprog1 = 1000/2kOhm = 500mA Timer disabled Charger always enabled THERM curr = 50uA, shutdown happens at 1.24V and 0.25V (Thermal shutoff at ~55 C, see NTC RT Calculations Excel sheet in project Github folder)
VBATT_CURR_SENSE = Iout*R3*100V/V = (5V-0.02V) max = 4.98V max I_max_sense = (4.98V)/(20mR*100V/V) = 2.49A

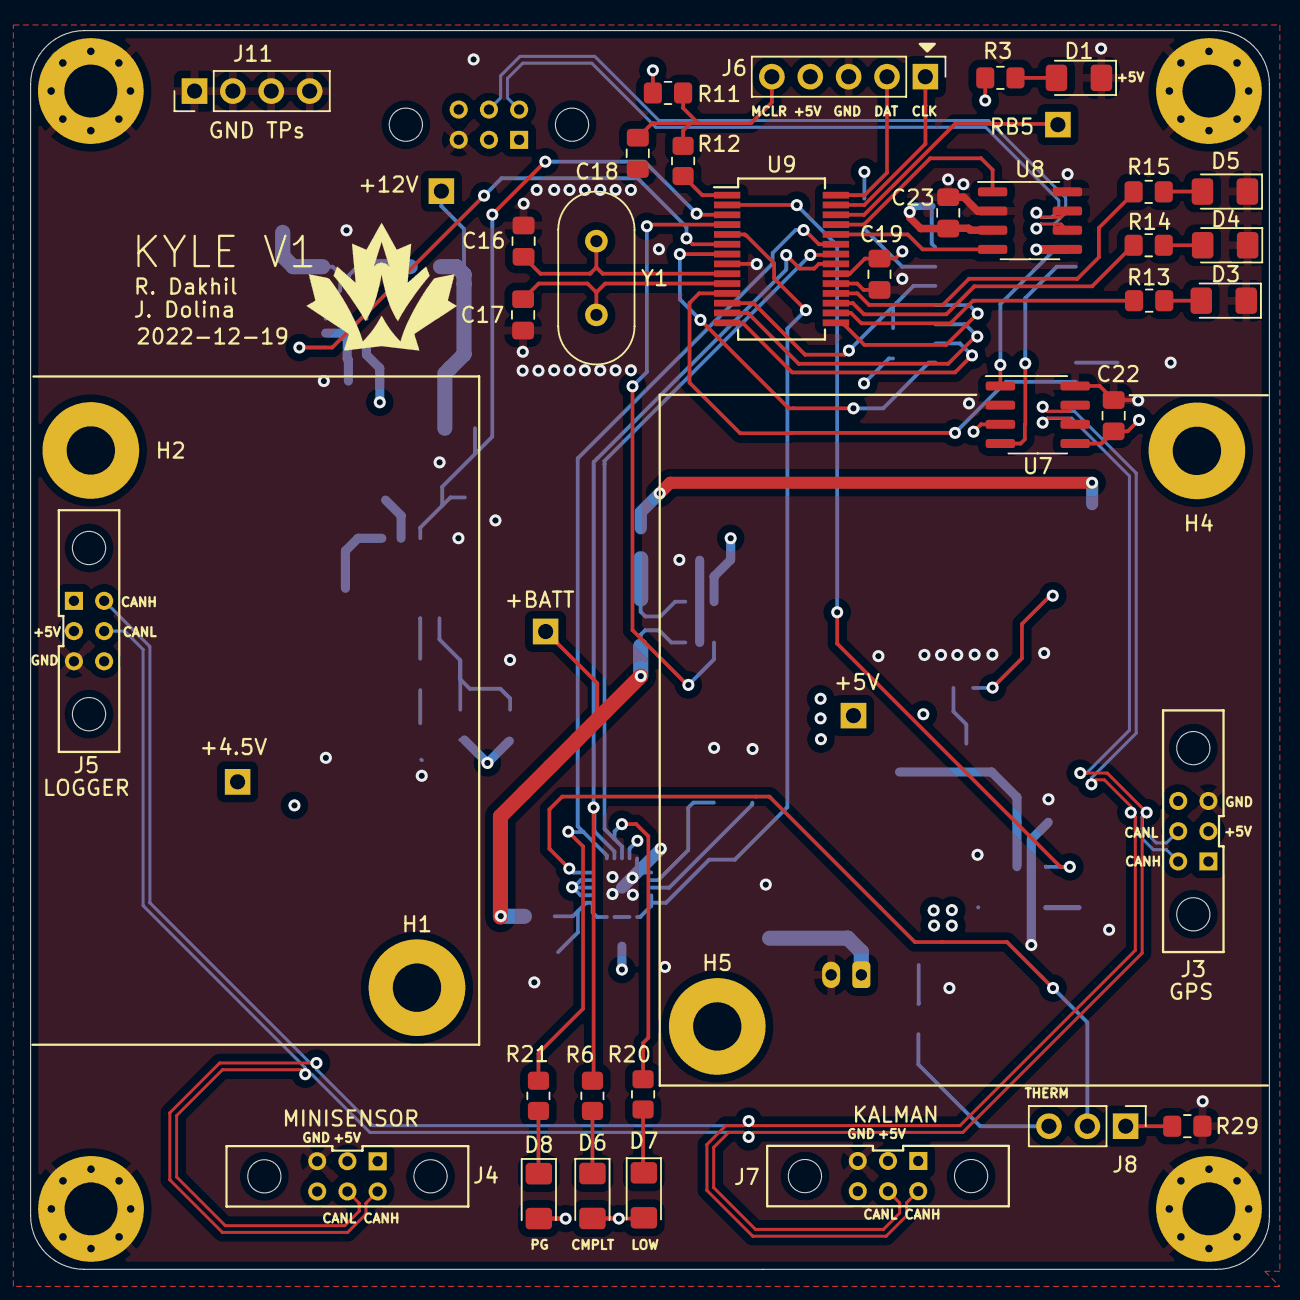
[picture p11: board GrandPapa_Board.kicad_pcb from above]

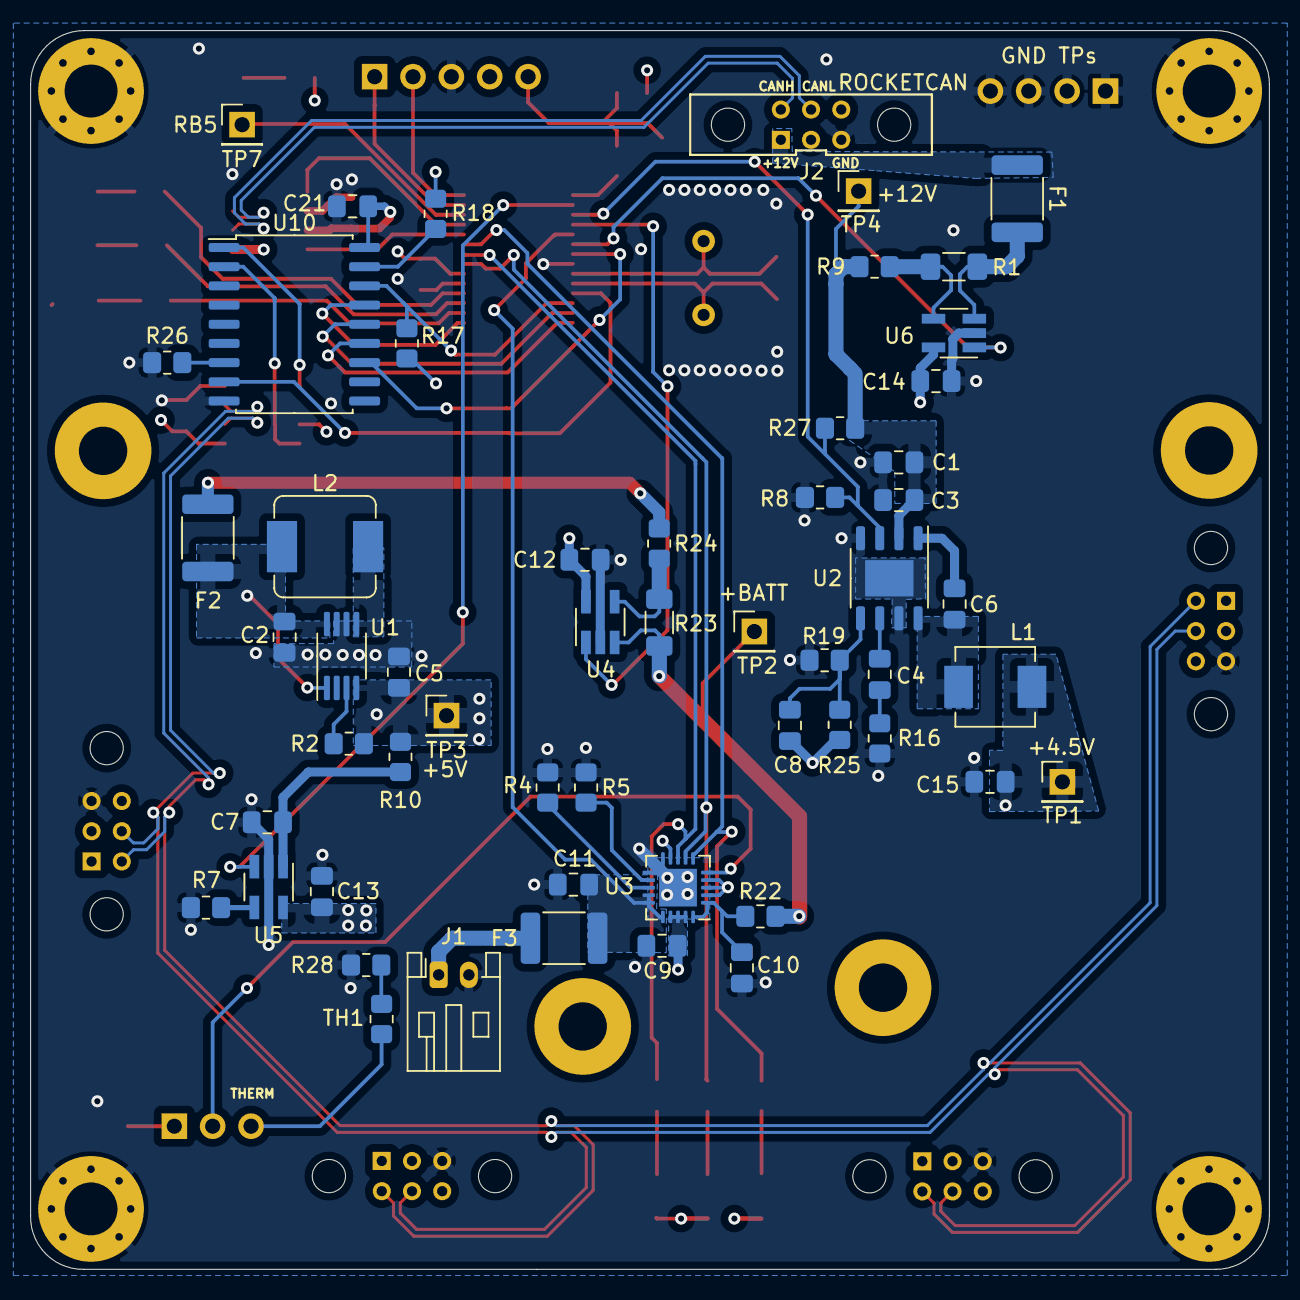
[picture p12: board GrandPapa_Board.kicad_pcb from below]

Board: 4 copper layers, 82.0 x 82.0 mm, 97 parts (55 on the bottom side), 70 nets.

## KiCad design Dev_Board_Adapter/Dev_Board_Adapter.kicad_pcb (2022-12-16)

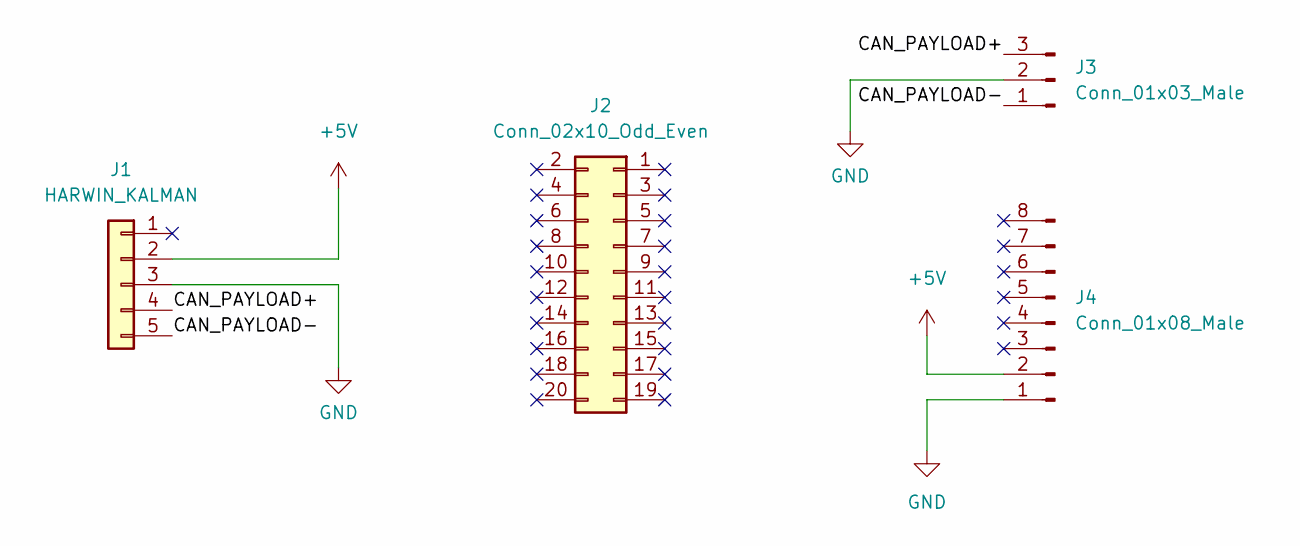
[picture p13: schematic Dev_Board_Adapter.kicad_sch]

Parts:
J1: HARWIN_KALMAN; connector_Harwin_M80-5000642
J2: Conn_02x10_Odd_Even; PinHeader_2x10_P2.54mm_Vertical
J3: Conn_01x03_Male; PinHeader_1x03_P2.54mm_Vertical
J4: Conn_01x08_Male; PinHeader_1x08_P2.54mm_Vertical

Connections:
+5V: J1.2, J4.2
/CAN_PAYLOAD+: J1.4, J3.3
/CAN_PAYLOAD-: J1.5, J3.1
GND: J1.3, J3.2, J4.1

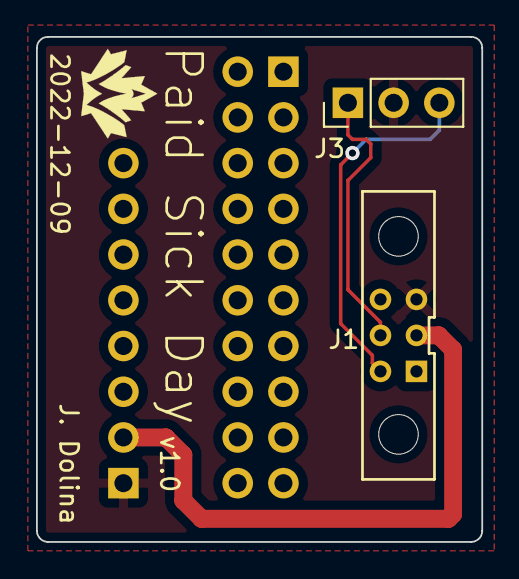
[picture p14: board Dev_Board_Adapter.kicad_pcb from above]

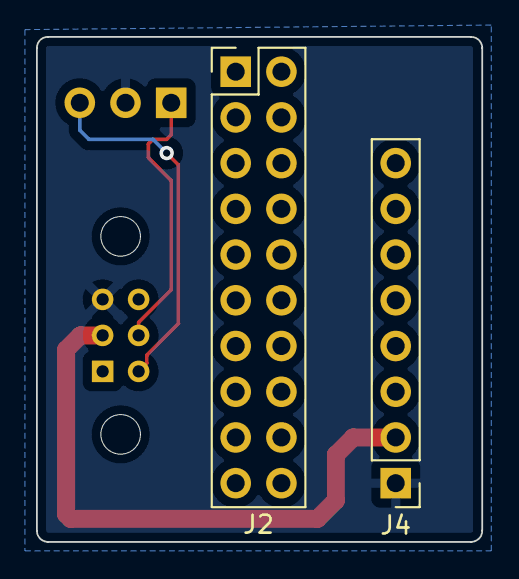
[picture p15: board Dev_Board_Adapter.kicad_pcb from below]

Board: 2 copper layers, 24.7 x 28.1 mm, 4 parts (2 on the bottom side), 4 nets.

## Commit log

2022-09-25 Init Grandpapa project files, updated README
    [GrandPapa_Board.kicad_pcb, GrandPapa_Board.kicad_sch, grandpapa_MCU.kicad_sch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]
2022-09-26 Shameless papa copying pt 1
    [GrandPapa_Board.kicad_sch, grandpapa_MCU.kicad_sch, grandpapa_Power.kicad_sch]
2022-09-27 Add power circuits and some PIC stuff, grandpapa lib
    5V buck, 3.3V LDO, load switches, current and voltage sensing, some PIC stuff
    [GrandPapa_Board.kicad_sch, grandpapa_MCU.kicad_sch, grandpapa_Power.kicad_sch]
2022-09-27 Add missing capacitor value, annotate symbols
    [GrandPapa_Board.kicad_sch, grandpapa_MCU.kicad_sch, grandpapa_Power.kicad_sch]
2022-09-27 Add motor current sense amp and board output connections
    [GrandPapa_Board.kicad_sch, grandpapa_MCU.kicad_sch, grandpapa_Power.kicad_sch]
2022-09-27 Add MCP2515, MCU pin naming scheme
    [GrandPapa_Board.kicad_sch, grandpapa_MCU.kicad_sch]
2022-09-28 Add INA180 to symbol lib, update 5v switch labels
    [GrandPapa_Board.kicad_sch, grandpapa_Charging.kicad_sch, grandpapa_MCU.kicad_sch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]
2022-09-29 Add FETs to power lines
    [GrandPapa_Board.kicad_sch, grandpapa_MCU.kicad_sch, grandpapa_Power.kicad_sch]
2022-09-30 clean up schematic, edit nets for clarification, add gnd test points, edit load switching scheme
    [GrandPapa_Board.kicad_sch, grandpapa_MCU.kicad_sch, grandpapa_Power.kicad_sch]
2022-10-09 Remove 3.3V, placeholders for battery charge IC and 5V boost converter
    [GrandPapa_Board.kicad_sch, grandpapa_MCU.kicad_sch, grandpapa_Power.kicad_sch]
2022-10-16 added MCP73871
    [GrandPapa_Board.kicad_sch, grandpapa_Power.kicad_sch]
2022-10-17 add 5V boost converter and 12V load switch, finish battery charge circuit
    [GrandPapa_Board.kicad_sch, grandpapa_MCU.kicad_sch, grandpapa_Power.kicad_sch]
2022-10-17 add missing datasheets
    [grandpapa_Power.kicad_sch]
2022-10-22 clean up schematic, fix some ERC errors
    [GrandPapa_Board.kicad_sch, grandpapa_MCU.kicad_sch, grandpapa_Power.kicad_sch]
2022-10-26 move 12V shutoff to reg, rm motor stuff, subsheet/global pin redesign
    [GrandPapa_Board.kicad_sch, grandpapa_Charge.kicad_sch, grandpapa_MCU.kicad_sch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]
2022-10-26 fix erc
    [GrandPapa_Board.kicad_sch, grandpapa_Charge.kicad_sch, grandpapa_MCU.kicad_sch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]
2022-10-30 fix SHDN pin config on 4.5V regulator
    [GrandPapa_Board.kicad_sch, grandpapa_Charge.kicad_sch, grandpapa_MCU.kicad_sch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]
2022-10-31 Addressed some Jack comments. 3/4/6/7 TBD
    [GrandPapa_Board.kicad_sch, grandpapa_Charge.kicad_sch, grandpapa_Power.kicad_sch]
2022-11-03 address the rest of jack's review, still need to fix grid spacing
    [GrandPapa_Board.kicad_sch, grandpapa_Charge.kicad_sch, grandpapa_MCU.kicad_sch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]
2022-11-06 fix disconnected pins, connect new hierarchical pins, misc layout changes
    [GrandPapa_Board.kicad_sch, grandpapa_Charge.kicad_sch, grandpapa_MCU.kicad_sch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]
2022-11-07 minor fixes; chip shortage tearing me a new one
    [GrandPapa_Board.kicad_sch, grandpapa_Charge.kicad_sch, grandpapa_MCU.kicad_sch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]
2022-11-10 added new buck reg IC, external component values TBA
    [GrandPapa_Board.kicad_sch, grandpapa_Charge.kicad_sch, grandpapa_MCU.kicad_sch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]
2022-11-12 more buck conv component sizing
    [GrandPapa_Board.kicad_sch, grandpapa_Power.kicad_sch]
2022-11-12 component sizing for 4.5V buck complete
    [GrandPapa_Board.kicad_sch, grandpapa_Power.kicad_sch]
2022-11-13 Addded 5V boost and kalman board connector
    [GrandPapa_Board.kicad_sch, grandpapa_Power.kicad_sch]
2022-11-13 minor changes, change some buck converter component values, add inductor + LED part numbers
    [GrandPapa_Board.kicad_sch, grandpapa_Charge.kicad_sch, grandpapa_MCU.kicad_sch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]
2022-11-16 fix 4.5V buck reg enable pin
    [GrandPapa_Board.kicad_sch, grandpapa_Power.kicad_sch]
2022-11-16 fix comments
    [GrandPapa_Board.kicad_sch, grandpapa_Charge.kicad_sch, grandpapa_MCU.kicad_sch]
2022-11-19 Add footprints, inductors TBD
    [GrandPapa_Board.kicad_sch, grandpapa_Charge.kicad_sch, grandpapa_MCU.kicad_sch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]
2022-11-20 Finish footprints, add board outline
    [GrandPapa_Board.kicad_pcb, GrandPapa_Board.kicad_sch, grandpapa_MCU.kicad_sch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]
2022-11-20 add footprints, group layouts
    [GrandPapa_Board.kicad_pcb, GrandPapa_Board.kicad_sch, grandpapa_Power.kicad_sch]
2022-11-23 change stackup, mounting holes, connector footprints, power reg layout, fuse values
    [GrandPapa_Board.kicad_pcb, GrandPapa_Board.kicad_sch, grandpapa_Charge.kicad_sch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]
2022-12-03 add footprint library
2022-12-03 4 straight hours of traces
    [GrandPapa_Board.kicad_pcb, GrandPapa_Board.kicad_sch, grandpapa_Power.kicad_sch]
2022-12-07 update layout + routing
    [GrandPapa_Board.kicad_pcb, GrandPapa_Board.kicad_sch, grandpapa_MCU.kicad_sch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]
2022-12-07 Fix silkscreen; add logo
    [GrandPapa_Board.kicad_pcb, GrandPapa_Board.kicad_sch, grandpapa_Charge.kicad_sch]
2022-12-08 Fix DRC errors
    [GrandPapa_Board.kicad_pcb, GrandPapa_Board.kicad_sch]
2022-12-08 undo errant schematic changes
    [GrandPapa_Board.kicad_sch]
2022-12-09 fix U8 pin 6 connection
    [GrandPapa_Board.kicad_sch, grandpapa_Charge.kicad_sch, grandpapa_MCU.kicad_sch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]
2022-12-09 Add R28 to fix thermal shdn; Add BOM and thermistor calc sheets
    [GPapa BOM.xlsx, GrandPapa_Board.kicad_pcb, GrandPapa_Board.kicad_sch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]
2022-12-09 Create schematic; exact layout TBD
    [Dev_Board_Adapter.kicad_pcb, Dev_Board_Adapter.kicad_sch]
2022-12-09 Fix silkscreen
    [Dev_Board_Adapter.kicad_pcb]
2022-12-10 fix spacing
    [Dev_Board_Adapter.kicad_pcb]
2022-12-10 fix edge cuts
    [Dev_Board_Adapter.kicad_pcb]
2022-12-10 Cleanup spacing, edges, corners
    [Dev_Board_Adapter.kicad_pcb]
2022-12-10 Fix corners for real
    [Dev_Board_Adapter.kicad_pcb]
2022-12-10 Add logo n stuff; front pour
    [Dev_Board_Adapter.kicad_pcb]
2022-12-10 Generate gerbers
    [Dev_Board_Adapter-B_Cu.gbr, Dev_Board_Adapter-B_Mask.gbr, Dev_Board_Adapter-B_Silkscreen.gbr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]
2022-12-10 fix gitignore, update BOM
    [GPapa BOM.xlsx]
2022-12-10 Add jumper to bypass thermal shutdown
    [GrandPapa_Board.kicad_pcb, GrandPapa_Board.kicad_sch, grandpapa_Charge.kicad_sch]
2022-12-12 minor PCB changes, fix logger mounting hole placement, minor schematic cleanup
    [GrandPapa_Board.kicad_pcb, GrandPapa_Board.kicad_sch, grandpapa_Charge.kicad_sch]
2022-12-12 fix battery LED indicator labels
    [GrandPapa_Board.kicad_pcb]
2022-12-13 Address Jack's comments, minor schematic text cleanup
    [GrandPapa_Board.kicad_pcb, GrandPapa_Board.kicad_sch, grandpapa_Charge.kicad_sch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]
2022-12-13 missed F3, update PDF
    [GrandPapa_Board.kicad_pcb, GrandPapa_Board.kicad_sch, grandpapa_Charge.kicad_sch]
2022-12-13 Generate STEP file
    [GrandPapa_Board.csv, GrandPapa_Board.step]
2022-12-15 Update BOM for ordering
    [GPapa BOM.xlsx, GrandPapa_Board.csv]
2022-12-16 flip Harwin; regen gerbers; add PDF
2022-12-16 gerbers, take 2
    [Dev_Board_Adapter-B_Cu.gbr, Dev_Board_Adapter-B_Mask.gbr, Dev_Board_Adapter-B_Silkscreen.gbr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]
2022-12-17 Move/rotate Harwins
    [GPapa BOM.xlsx, GrandPapa_Board.kicad_pcb]
2022-12-17 route CAN diff pairs, generate gerbers
    [GrandPapa_Board-B_Cu.gbr, GrandPapa_Board-B_Mask.gbr, GrandPapa_Board-B_Silkscreen.gbr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]
2022-12-20 Fix ur gitignore
    [GrandPapa_Board.csv]
2022-12-20 Finalize date on sikscreen; regen gerbers
    [GrandPapa_Board-B_Cu.gbr, GrandPapa_Board-B_Mask.gbr, GrandPapa_Board-B_Silkscreen.gbr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]
